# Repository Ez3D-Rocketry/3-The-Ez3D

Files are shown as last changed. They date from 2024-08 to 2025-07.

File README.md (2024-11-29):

# Ez3D
## 3D printed parts for a rocket that flies on A thru C motors

# Parts List:
1. Ez3D-1850-4 Fin Can
2. BT50 Nose Cone
3. 18mm Retainer Cap
   - Print out the multiple sizes (No scaling, +3%, +5%), These account for different printing tolerances and post flight shrinking.
4. BT50 3D printed Launch Lug assembly
5. Nine (9) inches of BT-50 type body tube
   - A standard 18 inch tube makes two kits
   - 3D printable tube cutting guide included in repository files
6. Three (3) feet of Kevlar string for Recovery Harness
   - Flight tested on 9KM DWLIFE Black Braided Kevlar Cord (1.3mm, 300 lb) but others may work
7. Twelve (12) inch parachute (Streamer can also be used but it descends fast)
8. Two (2) inches of BT-20 type body tube (Optional)
    - This tube serves as an Insulator between the motor and Fin Can
    - Use of Insulator helps reduce Fin Can heat shrink after each launch
9. Tape



# Assembly: 

1. Tie Recovery Harness to hole in Fin Can
2. Thread Recovery Harness thru Body Tube
3. Slide Body Tube onto top of Fin Can
4. Tape Body Tube to Fin Can - avoid blocking integrated launch lug
5. Tape Launch Lug Assembly midway up Body Tube
6. Tie loose end of Recovery Harness to Nose Cone
7. Attach parachute to Recovery Harness

**NOTE: Individual printers and filament have different tolerances** <br />
**- Fit check items before assembly. Options to adjust if necessary:**
- Add tape to increase diameter
- Remove material by sanding
- If your printer has a scaling feature, use it to adjust the part size
- Change the dimensions in the FreeCAD file available
  


# Launch Preparation:
1. Insert 1 or 2 squares of recovery wadding into Body Tube
2. Load Recovery Harness and Parachute into Body Tube
3. Place Nose Cone on top of Body Tube - ensure slightly snug fit
4. Slide BT-20 insulator into Fin Can before motor (Optional)
5. Load motor into Fin Can
    - Motor will fit loosely if BT-20 insulator is not used
    - Loose fit is not an issue with proper motor retention
7. Screw Motor Retention Cap onto base of Fin Can
   - Depending on your printer, the larger sizes may fit better
   - After a flight or two, the smaller size may fit better
9. Launch using standard model rocket procedures

# Recommended motors and expected performance: 

A8-3         = ~150 ft  (Optimum delay = 2.9 s)

B6-4         = ~300 ft (Optimum delay = 4.3 s)

C6-5         = ~600 ft (Optimum delay = 5.3 s)

# IMPORTANT POST FLIGHT NOTES:
- 3D printed material shrinks after cooling down from heat of motor
- Removal of motor may be difficult or impossible after one or several flights
- The smaller motor retainer cap may fit better after the first flight
- If existing motor retainer caps no longer work, friction or tape may suffice for retention
- PLA filament most suspectable to shrinking. Others may last longer.

## Entire kit fits in a gallon sized ziplock bag!


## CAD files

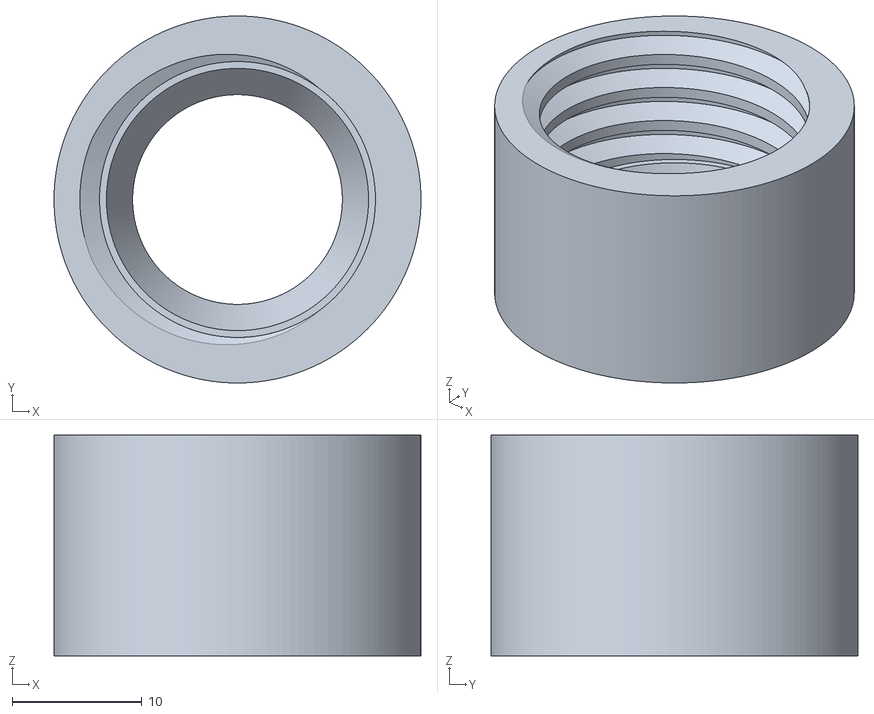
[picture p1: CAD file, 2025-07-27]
3D Printing Files/18mm Retainer Cap M24x3-17mmTall x1.01 in X and Y.stl
28.3 x 28.3 x 17.0

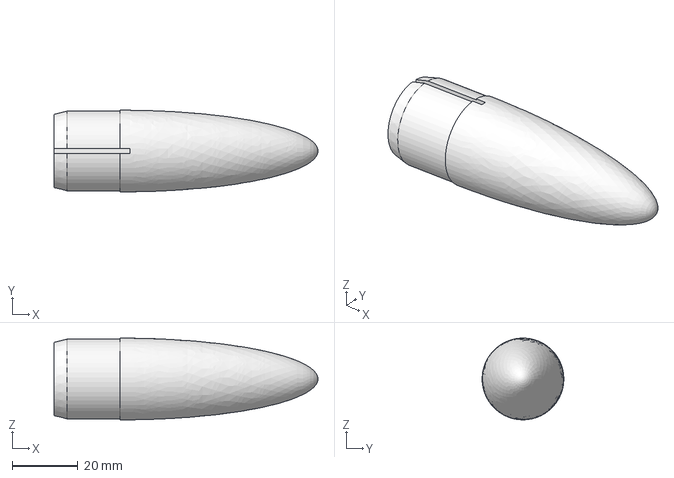
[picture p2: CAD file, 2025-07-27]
FreeCAD Files/BT50 Nose Cone - Elliptical, Hollow, with slot.FCStd
80.0 x 24.8 x 24.8 mm

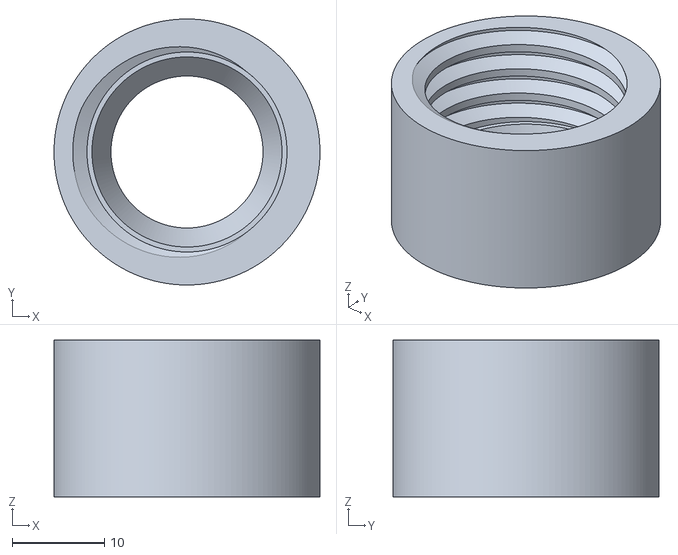
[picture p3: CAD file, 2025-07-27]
3D Printing Files/18mm Retainer Cap M24x3-17mmTall x1.03 in X and Y.stl
28.8 x 28.8 x 17.0

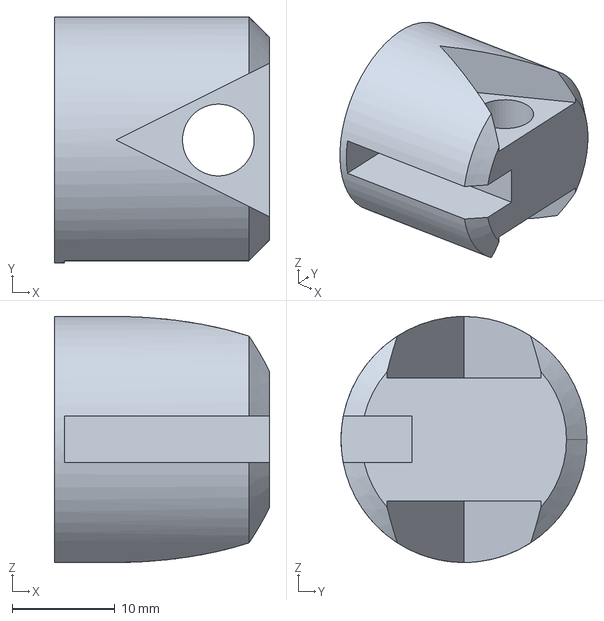
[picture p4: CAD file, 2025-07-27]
FreeCAD Files/BT50 Nose Cone - Elliptical, Solid, with slot.FCStd
21.0 x 24.0 x 24.0 mm

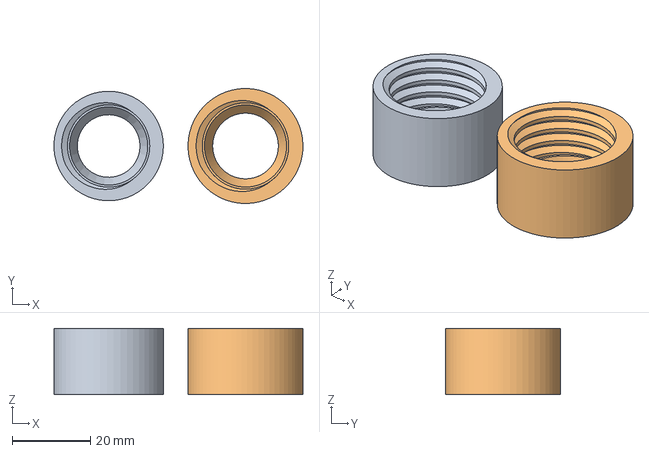
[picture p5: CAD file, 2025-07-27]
FreeCAD Files/18mm Retainer Cap M24x3-17mmTall.FCStd
63.7 x 29.4 x 17.0 mm
Use this Clone to make scaled up versions

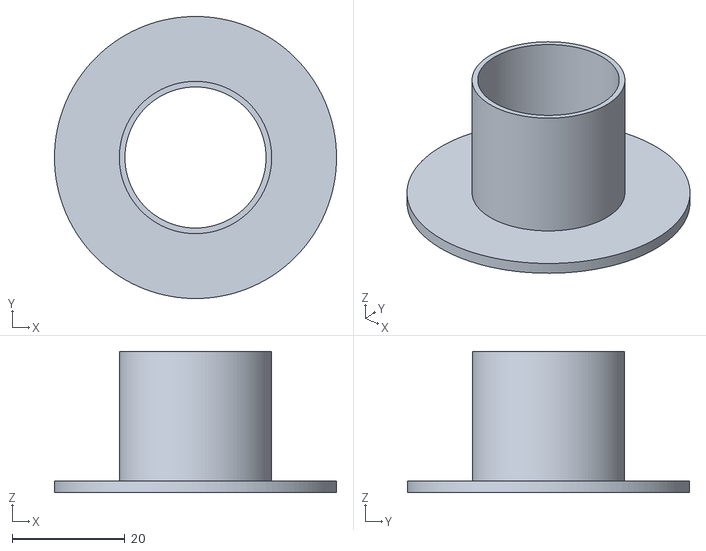
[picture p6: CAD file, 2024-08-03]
3D Printing Files/BT50 Tube Cutting Guide.stl
50.0 x 50.0 x 25.0

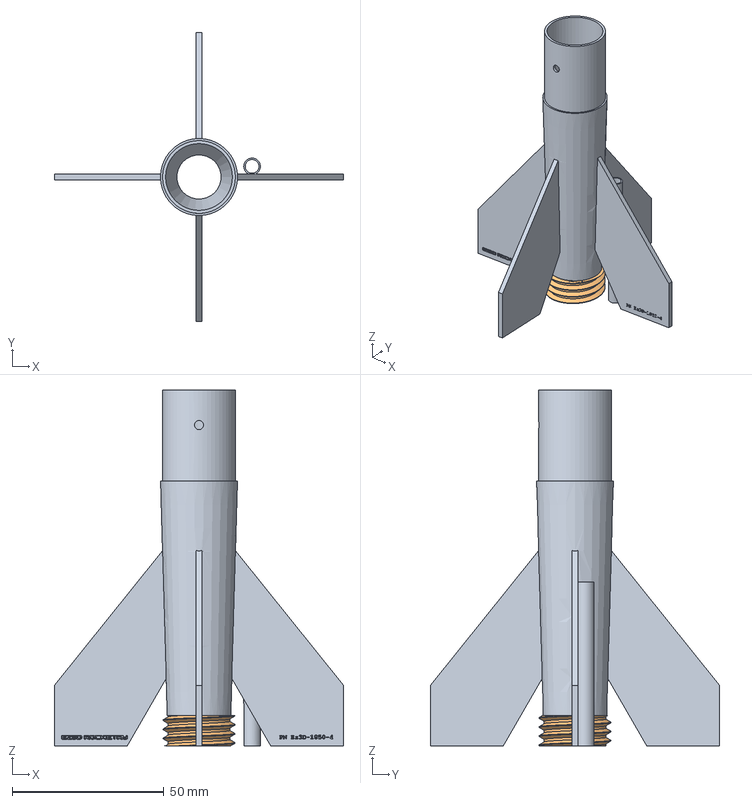
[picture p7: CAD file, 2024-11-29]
FreeCAD Files/Ez3D-1850-4 Fin Can.FCStd
95.3 x 95.3 x 117.4 mm
Thread-24x3-9.5Rad-10mmTall v1

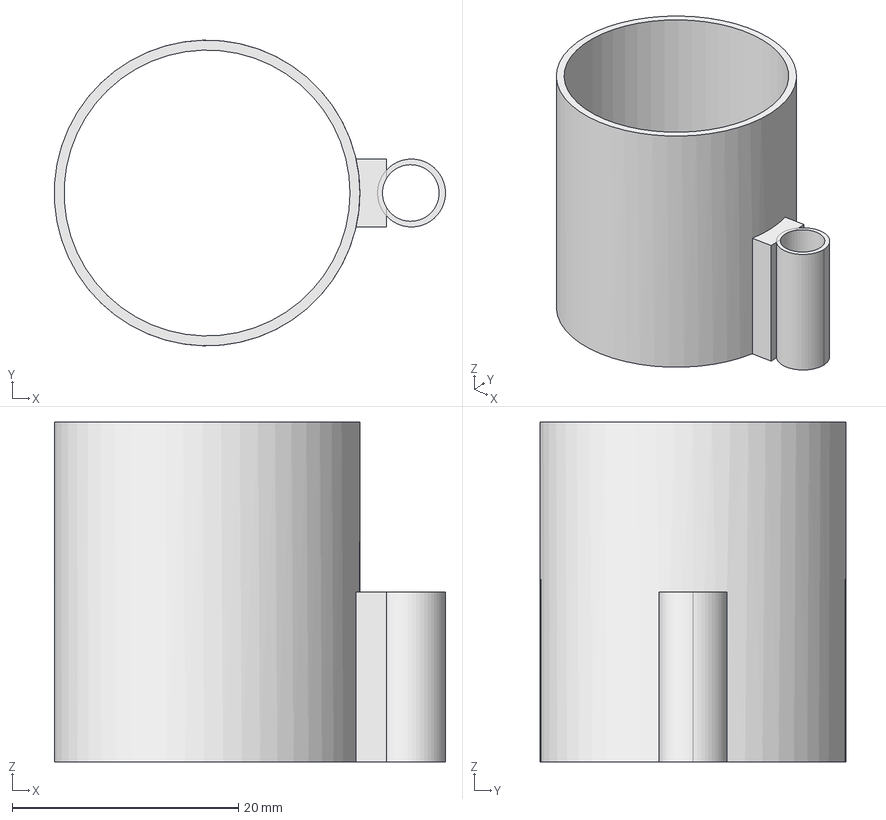
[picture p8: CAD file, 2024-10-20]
FreeCAD Files/BT50 Launch Lug.FCStd
34.5 x 27.0 x 30.0 mm

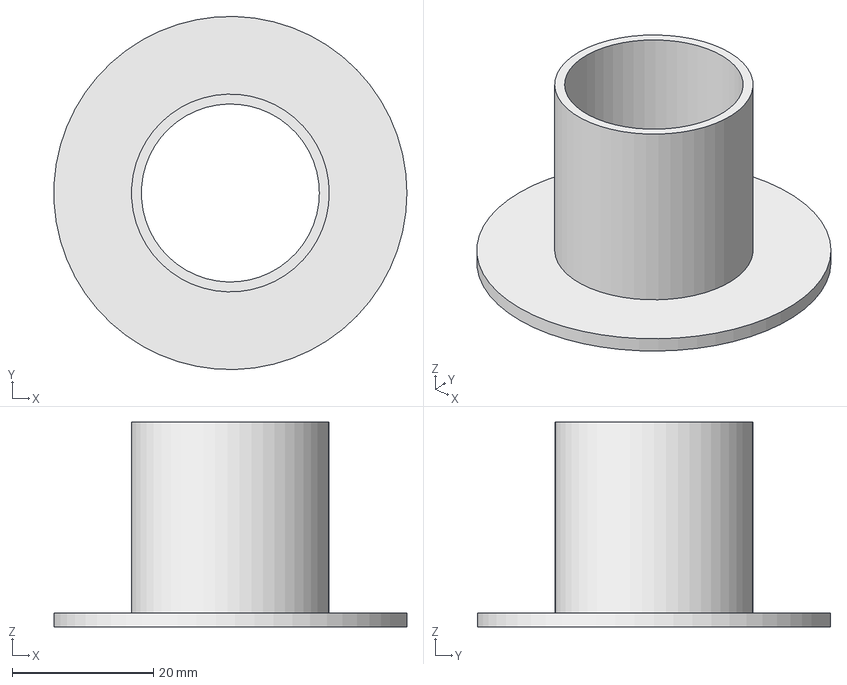
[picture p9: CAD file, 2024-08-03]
FreeCAD Files/BT50 Tube Cutter Guide.FCStd
50.0 x 50.0 x 29.0 mm

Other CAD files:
3D Printing Files/BT50 Launch Lug.stl
3D Printing Files/BT50 Nose Cone - Elliptical, Hollow, with slot.stl
3D Printing Files/BT50 Nose Cone - Elliptical, Solid, with slot.stl
3D Printing Files/Ez3D-1850-4 Fin Can.stl

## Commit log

2024-07-24 Ez3D Fin Can STL file
    [Ez3D Fin Can.stl]
2024-07-24 Ez3D Fin Can FreeCAD File
    [Ez3D Fin Can.FCStd]
2024-07-24 BT50 Nose Cone Hollow STL file
    [BT50 Nose Cone - simple threading hole.stl]
2024-07-24 BT50 Nose Cone hollow FreeCAD file
    [BT50 Nose Cone - simple threading hole.FCStd]
2024-07-24 BT50 Nose Cone - Solid - STL file
    [BT50 Nose Cone - solid with threading hole in base.stl]
2024-07-24 BT50 Nose Cone - solid - FreeCAD file
    [BT50 Nose Cone - solid with threading hole in base.FCStd]
2024-07-24 Motor Retainer Cap - 18mm 1.00 no scaling up STL file
    [18mm Retainer Cap original 1.00 size.stl]
2024-07-24 18mm motor retainer cap - original 1.00 size FreeCAD
    [18mm Retainer Cap original 1.00 size.FCStd]
2024-07-24 18mm Motor Retainer - scaled up 5% in X and Y STL file
    [18mm Motor Retainer Cap scaled 105 percent in X and Y.stl]
2024-07-25 BT50 Launch Lug STL file
    [BT50 Launch Lug-Body.stl]
2024-07-25 BT50 Launch Lug FreeCAD file
    [BT50 Launch Lug.FCStd]
2024-08-03 BT20 Tube Cutter Guide STL file
    [BT20 Tube Cutter Guide.stl]
2024-08-03 BT20 Tube Cutter Guide FreeCad fild
    [BT20 Tube Cutter Guide.FCStd]
2024-08-03 BT50 Tube Cutter STL file
    [BT50 Tube Cutting Guide.stl]
2024-08-03 BT50 Tube Cutter Guide FreeCAD file
    [BT50 Tube Cutter Guide.FCStd]
